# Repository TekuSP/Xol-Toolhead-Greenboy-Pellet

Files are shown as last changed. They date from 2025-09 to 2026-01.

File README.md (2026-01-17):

[][cc-by-nc-sa]

# Xol Toolhead
Xol Toolhead is the evolution of 'Mantis Xol 2' (<https://github.com/Armchair-Engineering/Mantis-Xol>).<br/>
Aimed at modularity and quality of life improvements for installation and serviceability.<br/>
We have left the mantis carriage behind, and thus are now just Xol sans Mantis. Don't worry, it's still a bit ugly. We wouldn't fix that..<br/>

This is fork for **Greenboy3D Pellet Extruder.** More about extruder here: https://greenboy3d.de <br/>

Project lead: ko-fi (https://ko-fi.com/O5O5OCC0K) [DW-Tas](https://github.com/DW-Tas)
Fork lead:  [TekuSP](https://github.com/TekuSP)

Join me on Discord (https://discord.gg/armchairengineeringsux)

Chat with me, fork owner on Discord: @TekuSP there



## Go to the /docs
All of the documentation has been moved to /docs to help keep the repo organised (crazy I know) and enable future things.
* [Full README](docs/README.md)
  * [Bill of Materials (BOM)](docs/BOM.md)
  * [Printing parts](docs/printing.md)
  * [Carriage assembly](docs/xol_carriage_assembly.md)
  * [Toolhead assembly](docs/toolhead_assembly.md)

<br/><br/>
You can help support the development of Armchair projects.<br/>
Donate at https://ko-fi.com/armchair<br/>
ko-fi (https://ko-fi.com/armchair)
<br/> <br/>

This work is licensed under a
[Creative Commons Attribution-NonCommercial-ShareAlike 4.0 International License][cc-by-nc-sa].

[][cc-by-nc-sa]

[cc-by-nc-sa]: http://creativecommons.org/licenses/by-nc-sa/4.0/
[cc-by-nc-sa-image]: https://licensebuttons.net/l/by-nc-sa/4.0/88x31.png
[cc-by-nc-sa-shield]: https://img.shields.io/badge/License-CC%20BY--NC--SA%204.0-lightgrey.svg

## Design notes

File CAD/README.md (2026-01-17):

The custom STLs that enable support for the Annex Double Folded Ascender are derived from an Annex Engineering design, they are bound by their license.
<br/><br/>
Additionally, the "assembly guide" CAD contains a mod of the Anex Sherpa-Mini which is also bound by their license.
<br/><br/>

Additionally, the "assembly guide" CAD contains a mod of the Greenboy3D pellet extruder model which is also bound by their license.
<br/><br/>The License Agreement for these "products" can be found here: https://github.com/Annex-Engineering/ANNEX-Engineering-License-Agreement
<br/><br/>
Product pages for these products can be found at:

* https://github.com/Annex-Engineering/Folded_Ascender-Extruder
* https://github.com/Annex-Engineering/Sherpa_Mini-Extruder
* https://wiki.greenboy3d.de/docs/Getting%20Started

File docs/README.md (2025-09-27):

[][cc-by-nc-sa]

# Xol Toolhead
Xol Toolhead is the evolution of 'Mantis Xol 2' (<https://github.com/Armchair-Engineering/Mantis-Xol>).<br/>
Aimed at modularity and quality of life improvements for installation and serviceability.<br/>
We have left the mantis carriage behind, and thus are now just Xol sans Mantis. Don't worry, it's still a bit ugly. We wouldn't fix that.

Project lead: ko-fi (https://ko-fi.com/O5O5OCC0K) [DW-Tas](https://github.com/DW-Tas)

Join me on Discord (https://discord.gg/armchairengineeringsux)



## What's new
`Xol-Toolhead Release [2024-06-19]`
### Major update
* Quality of life improvements
  * Toolhead
    * Combined multiple printed parts to simplify assembly
    * No more M2 or M2.5 heatset inserts
    * Part cooling fans slide into the top of the ducts are are secured with 2x M2.5x8 SHCS per fan
      * Hardware reduced from 8x M2 heatsets + 8 M2 screws to just 4 M2.5 screws
    * HE Fan now uses 4x M2.5x16 SHCS (previous M2.5x20 should still work)
    * All four hotend mounting screws can now be used with Rapido and Dragon UHF when using Sherpa-Mini Extruder
  * Carriage
    * Xol Carriage is now a single piece print
    * Belt clips are now the Archetype belt clip system
    * Internal path added for probe wires
* BOM changes
  * Toolhead
    * Removed:
      * M2 and M2.5 heatsets (except for X endstop)
      * M2 Screws (except for X endstop)
    * Extruder mount front 2 SHCS now 16mm (previously 20mm)
  * Carriage
    * All versions now attach to MGN rail with M3x8 SHCS (MGN12 previously required M3x6 BHCS)
    * Archetype belt clips require 4mm OD, 0.45mm wall width tube
      * 2x 22.5mm lengths
      * 'Has been tested with 4/3mm PTFE tube and seems OK but harder to install'
    * Belt pins are now all M3x30 for all carriage/belt combinations
      * Cut down screws now OK due to the metal tube protecting the belts
    * Added:
      * Large M3 washers and 2x M3x8 SHCS for MGN Carriage clamps (not optional, required for carriage strength)
* Tool Requirement
  * Tightening the M3 SHCS of the toolhead "feet" to the carriage requires a M2.5 ball head hex driver. `This is due to the requirement to tighten these screws from a slight angle.`
<details>
<summary><strong>Previous updates</strong> [click to expand]</summary>
<br/>

`Xol-Toolhead Release 2023-12-21`
[Historic Repo Link](https://github.com/Armchair-Heavy-Industries/Xol-Toolhead/tree/b5e52d79f11106338cad1ea619fc55be004061d5)
* Quality of life improvements
  * Cable routing holes are now on both sides of the toolhead
  * Cable routing holes can now fit MF3.0 commonly used on hotends
  * Awkward M3 Heatset insert replaced with easier to install M3 hex nut for front extruder mount connection
  * Rapido hotend mounting points rotated to improve wire routing
* Minimal BOM change
  * 1x M3 Hex Nut replaces 1x M3 Heatset Insert
  * 1x M3x6 BHCS replaces 1x M3x8 BHCS
* Reworked Extruder mount to Hotend mount interface
  * Old Hotend mounts will not work with new Extruder mounts and vice-versa

`Xol-Toolhead Release 2023-09-15`
[Historic Repo Link](https://github.com/Armchair-Heavy-Industries/Xol-Toolhead/tree/18acdc784e08c6703e5be316338cb8c8f26e0477)
* Modular approach to hotend mounts and extruders
  * Hotend mounts and extruder mounts are now separate parts
  * Extruder mounts incorporate the old Xol-Carriage or TAP adapter plates (same number of printed parts overall)
  * "Xol with bones" option: Add some screws for extra rigidity in the hotend mount
* Minimal BOM change
  * 1x M3x8 BHCS
  * 1x M3 Heatset
  * Optional "bones"
    * 2x M2x30 SHCS
    * 2x M2 Heatset
* Xol-Carriage update
  * Stronger belt clips
  * bigger probe cable channel with cable tie slot

`Xol-Toolhead Release 2023-07-14`
[Historic Repo Link](https://github.com/Armchair-Heavy-Industries/Xol-Toolhead/tree/bd63772155dfab692449fd498208c855561d44cf)
* Standardised hotend mounts around the Voron Design CW2/TAP carriage bolt hole pattern.
  * This approach reduces the number of hotend mounts and ducts by half - You don't have to search for TAP or non-TAP and we don't have to maintain twice as many parts
* Xol-Carriage
  * A new carriage built for Xol-Toolhead
  * Uses metal pins and a belt clip to secure the belts instead of having them squashed between mgn9/12 carriage and toolhead carriage
  * Improved serviceability - remove the toolhead from the carriage without disassembly in the printer. Unless you use Voron TAP or refuse to buy M2.5 hardware for Xol Carriage. Buy the m2.5 hardware, it's worth it trust us.
  * Modular probe mounting system - change probes without changing the whole carriage _`*Except for KlickyNG`_
* These carriage changes mean you can use any carriage that a Stealthburner bolts onto. (Our Xol-Carriage, or the stock voron carriage even.)
</details>

## Supported hardware
### Hotends
* Chube Compact
* Rapido HF
* Rapido UHF
* DropEffect XG
* DropEffect NeXtG
* Red Lizard K1-UHF
* Dragon UHF / UHF-Mini
* Dragon Standard / High Flow
* Dragon Ace
* Revo Voron
* NF-Crazy Volcano (or standard with v6 melt zone extender) `NF-Crazy with standard wide block no longer supported without extender`
* Others via User mods including [Bambulab](https://github.com/Armchair-Heavy-Industries/Armchair-Usermods/tree/main/files/Xol-Toolhead/BambuLab_Xol_HE_Mount)

### Extruders
* Sherpa-Mini
* Annex Double Folded Ascender
* Galileo G2SA *
* WristWatch G2 *
* WristWatch BMG
* Escapement (experimental)
* Vz-Hextrudort-Low
* LGX-Lite
* Orbiter v2.0

`⚠️ * G2SA and WWG2 not compatible with XolPAP `

### Probes
* PCB Klicky
* Klicky
* Beacon (Normal)
* Euclid
* Voron Design TAP `For RC8+ we suggest to use m3x50 BHCS instead of SHCS`<br/>
* BTT Eddy
* ⚠️ _KlickyNG support has been removed in this release_

### X-Rail/Belts
* MGN12H - 6mm Belts
* MGN12H - 9mm Belts
* MGN9H - 6mm Belts
* MGN9H - 9mm Belts

> [!WARNING]
> ## Front Idlers  
> Xol-Toolhead can collide with the stock voron front idlers for Trident and 2.4 when the toolhead is in the front corners of the build area. This can cause also issues with the homing sequence when homing X if the toolhead is at the front of the gantry on Y. <br/><br/>
> Fully compatible idlers:<br/>
> * clee's [BFI (Beefy Front Idlers)](https://github.com/clee/VoronBFI)  <br/>
> * Ramalama2's [Front Idlers](https://github.com/Ramalama2/Voron-2-Mods/tree/main/Front_Idlers)  

<br/>

> [!IMPORTANT]
> We've made some instructions for printing and assembly.  
> They took ages to make, please read them.  
> * [Bill of Materials (BOM)](BOM.md)  
> * [Printing parts](printing.md)  
> * [Carriage assembly](xol_carriage_assembly.md)  
> * [Toolhead assembly](toolhead_assembly.md)  
> * [LED Harness](led_harness.md)

## Acknowledgements
* [DW-Tas](https://github.com/DW-Tas) for giving Xol the giant refresh it needed.
* [CorvidBuilds](https://github.com/CorvidBuilds) for Xol1 and Xol2, the predecessors to this project.
* [Long/Mandryd](https://github.com/mandryd/VoronUsers/tree/master/printer_mods/Long/Mantis_Dual_5015) for the Mantis toolhead.
* [Derpimus](https://github.com/lraithel15133) for the exegesis, some CAD work, feedback, and just being a rad dude.
* [KayosMaker](https://github.com/KayosMaker) for the CAN board mounts and spacers.
* [JosAr](https://github.com/jlas1/Klicky-Probe) for Klicky.
* [WhoppingPochard](https://github.com/tanaes) and [VinnyCordeiro](https://github.com/VinnyCordeiro/) for PCB Klicky.
* [Nionio6915](https://github.com/nionio6915/Euclid_Probe) for Euclid.
* [VoronDesign](https://github.com/VoronDesign) for this particular CoreXY flavor.
* [AnnexEngineering](https://github.com/Annex-Engineering) for the Sherpa Mini and Double Folded Ascender extruders, and the K3 that influenced the air management of the ducts. And also for giving access to an early revision of the DFA so it could be adapted for this toolhead.
* [clee](https://github.com/clee), you know what you did.

<br/><br/>
You can help support the development of Armchair projects.<br/>
Donate at https://ko-fi.com/armchair<br/>
ko-fi (https://ko-fi.com/armchair)
<br/> <br/>

This work is licensed under a
[Creative Commons Attribution-NonCommercial-ShareAlike 4.0 International License][cc-by-nc-sa].

[][cc-by-nc-sa]

[cc-by-nc-sa]: http://creativecommons.org/licenses/by-nc-sa/4.0/
[cc-by-nc-sa-image]: https://licensebuttons.net/l/by-nc-sa/4.0/88x31.png
[cc-by-nc-sa-shield]: https://img.shields.io/badge/License-CC%20BY--NC--SA%204.0-lightgrey.svg

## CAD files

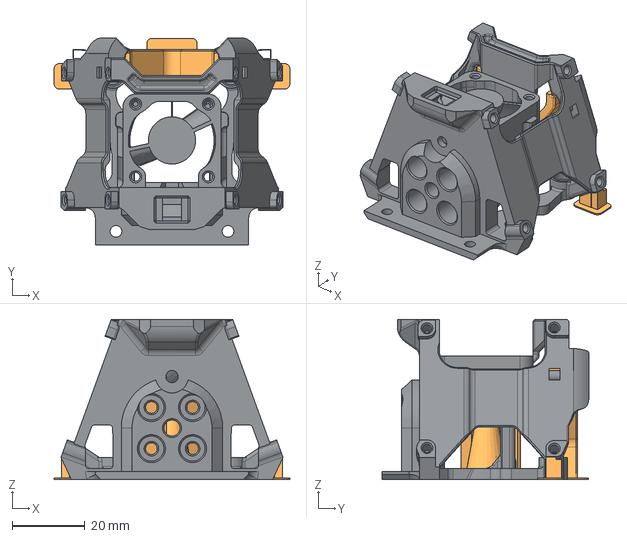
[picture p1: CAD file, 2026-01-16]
CAD/parts/Xol_HE_Chube-Compact_XolPAP.step
64.9 x 56.8 x 44.0 mm

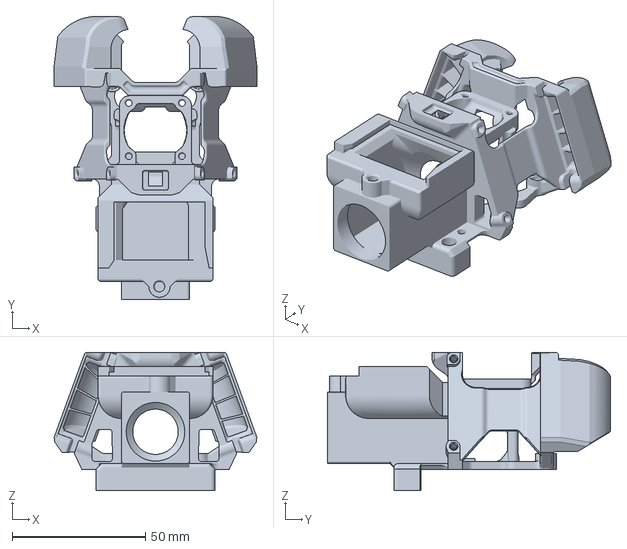
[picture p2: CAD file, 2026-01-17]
STL/Extruder Mounts/Xol Extruder Mount - Greenboy3D Pellet Extruder.3mf
76.2 x 106.3 x 52.0 mm

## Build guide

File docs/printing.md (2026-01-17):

# Printing Xol Parts

### Xol parts are not scaled to suit any particular filament. You will need to calibrate your printer/filament appropriately before printing Xol Parts

It is recommended to print a calibration part of a known size and adjust slicer shrinkage compensation.

### Printer tuning
Making Xol easier to assemble also meant making the main hotend mount part a more difficult print. You will need to have a reasonably well callibrated printer (although it was tested on a barely tuned Ender 3). <br/>
Some things in particular to note:
* Support removal `If you're printing too hot or with insufficient cooling the built in supports may be difficult to remove.`
* Overhangs `They're not too steep, but will be a problem if you're not printing your perimeters "inside to outside".`
* Wall widths `Some of the supports have a built in "interface" layers. Make sure your printer profile allows printing of walls down to at least 0.4mm. Check that you can see them in your slicer before you print them. DO NOT use walls wider than 0.55mm`

## What to print
There are many combinations of carriages/hotends/extruders that can be used with Xol. The tables below outline what you should print.

### Carriage
#### Xol Carriage
Pick the parts you need from the lists below and follow the instructions in [xol_carriage_assembly.md](xol_carriage_assembly.md) to build.

Carriage Size
* MGN12H: [Xol-Carriage_MGN12H.stl](../STL/Xol-Carriage/Xol-Carriage_MGN12H.stl)
* MGN9H: [Xol-Carriage_MGN9H.stl](../STL/Xol-Carriage/Xol-Carriage_MGN9H.stl)
* MGN9H (Front rail Printers for Ants [PFA]): [Xol-Carriage_MGN9H_PFA.stl](../STL/Xol-Carriage/Xol-Carriage_MGN9H_PFA.stl)

Belt Width
* 6MM: [[a]_belt_clamp_6mm_x2.stl](../STL/Xol-Carriage/[a]_belt_clamp_6mm_x2.stl)
* 9MM: [[a]_belt_clamp_9mm_x2.stl](../STL/Xol-Carriage/[a]_belt_clamp_9mm_x2.stl)
* 6MM (Front rail Printers for Ants [PFA]): [[a]_belt_clamp_6mm_PFA_x2.stl](../STL/Xol-Carriage/[a]_belt_clamp_6mm_PFA_x2.stl)

Probe Modules
* Pick the module to match your supported probe from the [Probe Modules](<../STL/Xol-Carriage/Probe Modules>) folder. <br/>
`Probe length should match the hotend length (standard or UHF)`

#### Voron Design TAP
Follow instructions from Voron Design <br /> _`For TAP RC8, replace the M3x50 SCHS with M3x50 BHCS to avoid bed clearance issues with regular length Xol Ducts`_

### Hotend and extruder hybrid Mount

| Hotend | 4010 Blower | XolPAP (Remote Cooling) | Duct Length (for probe module / XolPAP) |
| --- | --- | --- | --- |
| Greenboy3D Pellet Extruder | [Xol Extruder Mount - Greenboy3D Pellet Extruder.3mf](<../STL/Xol Extruder Mount - Greenboy3D Pellet Extruder.3mf>) | --- | UHF |

### Hotend Mount
Pick one option from the table below, depending of if you're using 4010 blower fans or remote cooling (XolPAP) for part cooling.

| Hotend | 4010 Blower | XolPAP (Remote Cooling) | Duct Length (for probe module / XolPAP) |
| --- | --- | --- | --- |
| Chube Compact | [Xol_HE_Mount-Chube-Compact_Fan.stl](<../STL/HE Mounts/Xol_HE_Mount-Chube-Compact_Fan.stl>) | [Xol_HE_Mount-Chube-Compact_XolPAP.stl](<../STL/HE Mounts/Xol_HE_Mount-Chube-Compact_XolPAP.stl>) | Standard |
| Rapido HF | [Xol_HE_Mount-Rapido_HF_Fan.stl](<../STL/HE Mounts/Xol_HE_Mount-Rapido_HF_Fan.stl>) <br/><br/> [Xol_HE_Mount-Rapido_v2_HF_Fan.stl](<../STL/HE Mounts/Xol_HE_Mount-Rapido_v2_HF_Fan.stl>) | [Xol_HE_Mount-Rapido_HF_XolPAP.stl](<../STL/HE Mounts/Xol_HE_Mount-Rapido_HF_XolPAP.stl>) <br/><br/> [Xol_HE_Mount-Rapido_v2_HF_XolPAP.stl](<../STL/HE Mounts/Xol_HE_Mount-Rapido_v2_HF_XolPAP.stl>) | Standard |
| Rapido UHF | [Xol_HE_Mount-Rapido_UHF_Fan.stl](<../STL/HE Mounts/Xol_HE_Mount-Rapido_UHF_Fan.stl>) <br/><br/> [Xol_HE_Mount-Rapido_v2_UHF_Fan.stl](<../STL/HE Mounts/Xol_HE_Mount-Rapido_v2_UHF_Fan.stl>) | [Xol_HE_Mount-Rapido_UHF_XolPAP.stl](<../STL/HE Mounts/Xol_HE_Mount-Rapido_UHF_XolPAP.stl>) <br/><br/> [Xol_HE_Mount-Rapido_v2_UHF_XolPAP.stl](<../STL/HE Mounts/Xol_HE_Mount-Rapido_v2_UHF_XolPAP.stl>) | UHF |
| DropEffect XG | [Xol_HE_Mount-XG_Fan.stl](<../STL/HE Mounts/Xol_HE_Mount-XG_Fan.stl>) | [Xol_HE_Mount-XG_XolPAP.stl](<../STL/HE Mounts/Xol_HE_Mount-XG_XolPAP.stl>) | Standard |
| DropEffect NeXtG (without extender) | [Xol_HE_Mount-DragonSF-HF_Fan.stl](<../STL/HE Mounts/Xol_HE_Mount-DragonSF-HF_Fan.stl>) | [Xol_HE_Mount-DragonSF-HF_XolPAP.stl](<../STL/HE Mounts/Xol_HE_Mount-DragonSF-HF_XolPAP.stl>) | Standard |
| DropEffect NeXtG (with extender) | [Xol_HE_Mount-DragonUHF_Mini_Fan.stl](<../STL/HE Mounts/Xol_HE_Mount-DragonUHF_Mini_Fan.stl>) | [Xol_HE_Mount-DragonUHF_Mini_XolPAP.stl](<../STL/HE Mounts/Xol_HE_Mount-DragonUHF_Mini_XolPAP.stl>) | Standard |
| Red Lizard K1-UHF | [Xol_HE_Mount-Rapido_UHF_Fan.stl](<../STL/HE Mounts/Xol_HE_Mount-Rapido_UHF_Fan.stl>) | [Xol_HE_Mount-Rapido_UHF_XolPAP.stl](<../STL/HE Mounts/Xol_HE_Mount-Rapido_UHF_XolPAP.stl>) | UHF |
| Dragon UHF | [Xol_HE_Mount-DragonUHF_Fan.stl](<../STL/HE Mounts/Xol_HE_Mount-DragonUHF_Fan.stl>) | [Xol_HE_Mount-DragonUHF_XolPAP.stl](<../STL/HE Mounts/Xol_HE_Mount-DragonUHF_XolPAP.stl>) | UHF |
| Dragon UHF-Mini (extender removed)  | [Xol_HE_Mount-DragonUHF_Mini_Fan.stl](<../STL/HE Mounts/Xol_HE_Mount-DragonUHF_Mini_Fan.stl>) | [Xol_HE_Mount-DragonUHF_Mini_XolPAP.stl](<../STL/HE Mounts/Xol_HE_Mount-DragonUHF_Mini_XolPAP.stl>) | Standard |
| Dragon Standard / High Flow | [Xol_HE_Mount-DragonSF-HF_Fan.stl](<../STL/HE Mounts/Xol_HE_Mount-DragonSF-HF_Fan.stl>) | [Xol_HE_Mount-DragonSF-HF_XolPAP.stl](<../STL/HE Mounts/Xol_HE_Mount-DragonSF-HF_XolPAP.stl>) | Standard |
| Dragon Ace (without extender) | [Xol_HE_Mount-Dragon-Ace_Fan.stl](<../STL/HE Mounts/Xol_HE_Mount-Dragon-Ace_Fan.stl>) | [Xol_HE_Mount-Dragon-Ace_XolPAP.stl](<../STL/HE Mounts/Xol_HE_Mount-Dragon-Ace_XolPAP.stl>) | Standard |
| Dragon Ace (with extender) | [Xol_HE_Mount-Dragon-Ace_Extender_Fan.stl](<../STL/HE Mounts/Xol_HE_Mount-Dragon-Ace_Extender_Fan.stl>) | [Xol_HE_Mount-Dragon-Ace_Extender_XolPAP.stl](<../STL/HE Mounts/Xol_HE_Mount-Dragon-Ace_Extender_XolPAP.stl>) | UHF |
| Dragon Ace Volcano (with extender)<br/>`Use included 3mm spacer` | [Xol_HE_Mount-DragonUHF_Fan.stl](<../STL/HE Mounts/Xol_HE_Mount-DragonUHF_Fan.stl>) | [Xol_HE_Mount-DragonUHF_XolPAP.stl](<../STL/HE Mounts/Xol_HE_Mount-DragonUHF_XolPAP.stl>) | UHF |
| Dragon Ace Volcano (No extender)<br/>`Use included 3mm spacer`  | [Xol_HE_Mount-DragonUHF_Mini_Fan.stl](<../STL/HE Mounts/Xol_HE_Mount-DragonUHF_Mini_Fan.stl>) | [Xol_HE_Mount-DragonUHF_Mini_XolPAP.stl](<../STL/HE Mounts/Xol_HE_Mount-DragonUHF_Mini_XolPAP.stl>) | Standard |
| Revo Voron | [Xol_HE_Mount-Revo-Voron_Fan.stl](<../STL/HE Mounts/Xol_HE_Mount-Revo-Voron_Fan.stl>) | [Xol_HE_Mount-Revo-Voron_XolPAP.stl](<../STL/HE Mounts/Xol_HE_Mount-Revo-Voron_XolPAP.stl>) | Standard |
| NF-Crazy Volcano | [Xol_HE_Mount-NF-Crazy_Volcano_Fan.stl](<../STL/HE Mounts/Xol_HE_Mount-NF-Crazy_Volcano_Fan.stl>) | [Xol_HE_Mount-NF-Crazy_Volcano_XolPAP.stl](<../STL/HE Mounts/Xol_HE_Mount-NF-Crazy_Volcano_XolPAP.stl>) | UHF |

#### XolPAP Ducts
If you're using XolPAP remote cooling, you will need either standard or UHF length ducts:
* Standard: [XolPAP Standard Length Duct.stl](<../STL/XolPAP ducts/XolPAP Standard Length Duct.stl>)
* UHF: [XolPAP UHF Length Duct.stl](<../STL/XolPAP ducts/XolPAP UHF Length Duct.stl>)

`⚠️ * G2SA and WWG2 extruders not compatible with XolPAP `

### Extruder Mount

Pick one extruder mount from the table below to match your extruder, and if it's going on Xol-Carriage or on TAP/Voron carriage.

| Extruder | Xol-Carriage | TAP / Voron Carriage |
| --- | --- | --- |
| Sherpa-Mini / <br/> Sharkfin  <br/>`K-face plate and optional` <br/> `short idler arm for Sherpa-Mini ` <br/> `from Annex Engineering`<br/> [Sherpa front k-face](<https://github.com/Annex-Engineering/Sherpa_Mini-Extruder/blob/master/STLs/optional_parts/%5Ba%5D_housing_front_k_x1_rev15.STL>) <br/> [Sherpa short idler arm](<https://github.com/Annex-Engineering/Sherpa_Mini-Extruder/blob/master/STLs/optional_parts/%5Ba%5D_idler_arm_short_x1_rev16a.STL>) | [Xol Extruder Mount - Sherpa-Mini.3mf](<../STL/Extruder Mounts/Xol Extruder Mount - Sherpa-Mini.3mf>) | [Xol Extruder Mount - Sherpa Mini - TAP.3mf](<../STL/Extruder Mounts/Xol Extruder Mount - Sherpa Mini - TAP.3mf>) |
| Annex Double Folded Ascender | [Xol Extruder Mount - DFA.stl](<../STL/Extruder Mounts/Xol Extruder Mount - DFA.stl>) <br/> *License [Note](<DFA_MOD_License.md>) | Not Supported |
| Vz-Hextrudort-Low / <br/> LGX-Lite | [Xol Extruder Mount - VZ-Hex+LGX-L.stl](<../STL/Extruder Mounts/Xol Extruder Mount - VZ-Hex+LGX-L.stl>) | [Xol Extruder Mount - VZ-Hex+LGX-L - TAP.stl](<../STL/Extruder Mounts/Xol Extruder Mount - VZ-Hex+LGX-L - TAP.stl>) |
| Galileo G2SA (Orbiter mount pattern) <br/> `NOT XolPAP Compatible` | [Xol Extruder Mount - G2SA.stl](<../STL/Extruder Mounts/Xol Extruder Mount - G2SA.stl>), AND <br/>  [G2SA front for Xol Extruder Mount.stl](<../STL/Extruder Mounts/G2SA front for Xol Extruder Mount.stl>) | [Xol Extruder Mount - G2SA - TAP.stl](<../STL/Extruder Mounts/Xol Extruder Mount - G2SA - TAP.stl>) , AND <br/>  [G2SA front for Xol Extruder Mount.stl](<../STL/Extruder Mounts/G2SA front for Xol Extruder Mount.stl>) |
| WristWatch G2 (Orbiter mount pattern)  <br/> `NOT XolPAP Compatible` | [Xol Extruder Mount - G2SA.stl](<../STL/Extruder Mounts/Xol Extruder Mount - G2SA.stl>), AND <br/>  [WWG2 front for Xol Extruder Mount.stl](<../STL/Extruder Mounts/WWG2 front for Xol Extruder Mount.stl>) | [Xol Extruder Mount - G2SA - TAP.stl](<../STL/Extruder Mounts/Xol Extruder Mount - G2SA - TAP.stl>) , AND <br/>  [WWG2 front for Xol Extruder Mount.stl](<../STL/Extruder Mounts/WWG2 front for Xol Extruder Mount.stl>) |
| WristWatch BMG | [Xol Extruder Mount - G2SA.stl](<../STL/Extruder Mounts/Xol Extruder Mount - G2SA.stl>), AND <br/>  [WWBMG front for Xol Extruder Mount.stl](<../STL/Extruder Mounts/WWBMG front for Xol Extruder Mount.stl>) | [Xol Extruder Mount - G2SA - TAP.stl](<../STL/Extruder Mounts/Xol Extruder Mount - G2SA - TAP.stl>) , AND <br/>  [WWBMG front for Xol Extruder Mount.stl](<../STL/Extruder Mounts/WWBMG front for Xol Extruder Mount.stl>) |
| Escapement | [Xol Extruder Mount - Escapement.stl](<../STL/Extruder Mounts/Xol Extruder Mount - Escapement.stl>) | [Xol Extruder Mount - Escapement - TAP.stl](<../STL/Extruder Mounts/Xol Extruder Mount - Escapement - TAP.stl>) |
| Orbiter v2.0 | [Xol Extruder Mount - Orbiter V2.stl](<../STL/Extruder Mounts/Xol Extruder Mount - Orbiter V2.stl>) | [Xol Extruder Mount - Orbiter V2 - TAP.stl](<../STL/Extruder Mounts/Xol Extruder Mount - Orbiter V2 - TAP.stl>) |

 ### Faceplate
There's only one option for the faceplate now. If you don't want an LED in the status light area, print the "diffuser" in a contrasting colour to the main faceplate part to show off the Xol logo.
* [Faceplate.stl](../STL/Faceplate/Faceplate.stl)
* [[t] Logo LED diffuser.stl](<../STL/Faceplate/[t] Logo LED diffuser.stl>) `Clear/translucent for diffuser, or contrasting colour for no LED`

 #### EBB 36 Mount
 Print the EBB 36 mount for Xol-Carriage to suit your CAN or break-out board / extruder combination.<br/>
 `If you aren't using Xol-Carriage (TAP users) there are numerous EBB mounts availble like these from KayosMaker:`[CANboard_Mounts](https://github.com/KayosMaker/CANboard_Mounts)
| Extruder | Without strain relief | With strain relief|
|-----|---|---|
|Sherpa-Mini |[EBB36 Mount - Sherpa-Mini.stl](<../STL/EBB Mounts/EBB36 Mount - Sherpa-Mini.stl>)|[EBB36 Mount - Sherpa-Mini [strain relief].stl](<../STL/EBB Mounts/EBB36 Mount - Sherpa-Mini [strain relief].stl>) |
|WW-BMG |[EBB36 Mount - WWBMG.stl](<../STL/EBB Mounts/EBB36 Mount - WWBMG.stl>)|[EBB36 Mount -WWBMG [strain relief].stl](<../STL/EBB Mounts/EBB36 Mount -WWBMG [strain relief].stl>)
|DFA | {todo} | {todo} |
| Galileo 2SA | {todo} | {todo} |
| Escapement | {todo} | {todo} |
|VZ-Hextrudort-Low | [EBB36 Mount - VZ-Hextrudort-Low.stl](<../STL/EBB Mounts/EBB36 Mount - VZ-Hextrudort-Low.stl>) | [EBB36 Mount - VZ-Hextrudort-Low [strain relief].stl](<../STL/EBB Mounts/EBB36 Mount - VZ-Hextrudort-Low [strain relief].stl>) |
| LGX-Lite | {todo} | {todo} |
|Orbiter v2.0 | [EBB36 Mount - Orbiter2.0.stl](<../STL/EBB Mounts/EBB36 Mount - Orbiter2.0.stl>) | [EBB36 Mount - Orbiter2.0 [strain relief].stl](<../STL/EBB Mounts/EBB36 Mount - Orbiter2.0 [strain relief].stl>) |

### M2.5 Savers
 Add a little colour, and protect your delicate 4010 blower fans <br/>
* [[a]_M2.5_saver_x4.stl](../STL/Faceplate/[a]_M2.5_saver_x4.stl) `These aren't optional extras, you need them to protect your fans. Also the screw holes are too shalow without them`

### Trident stepper spacer
On some Trident printers, the leadscrews are slightly too high and may collide with the Xol ducts when the toolhead is at the very front corners of the printer (usually only the right side when homing at Y,0). <br/>
To avoid this colision, there is a spacer available on printables that will lower the leadscrew stepper motors: [https://www.printables.com/model/486638-voron-trident-z-steppers-spacers](https://www.printables.com/model/486638-voron-trident-z-steppers-spacers)

<br/><br/><br/><br/>

⬅ [BOM](BOM.md) - [Carriage assembly](xol_carriage_assembly.md) ➡

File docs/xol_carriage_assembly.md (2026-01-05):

# Xol Carriage Assembly
Xol Carriage Image

| Notes | Image |
| --- | --- |
| Get the carriage ready by installing <br /> * 5x M3 heatsets<br />* 4x M3 hex nuts |  <br/>  <br/>  |
| Attach your probe module with 2x M3x6 BHCS |  |
| Run the probe wires up the channel before you install the carriage on the MGN rail. Don't forget to keep them secure using the cable tie slots. |  |
| `Option`<br/>_*If you haven't yet converted to sensorless homing, your X-endstop switch can be attached to the back of the carriage._<br/><br/> Install the switch with 2x M2x10 self tapping screws |  |
| Put the carriage on the MGN rail with <br />4 M3x8 SHCS<br/> `M3x6 for CNC Xol-Carraige` |  |
| Use 2x M3x8 SHCS and 2x large M3 washers to 'clamp' the carriage to the MGN rail. `M3 + M5 washers can be stacked if you don't have the large M3 washers` |  <br/>  |
| Install the belts and tubes into the belt clips. It should look like the picture when installed correctly.<br/> `Left clip hidden to show the belt path inside the clip` <br/> <br/>  * Pull your belt through the belt clips.<br/>  * Make a loop and pinch together so that the teeth are locking together.<br/>  * Pull the belt back through the same hole in the clip.<br/>  * Repeat for the 2nd belt, leaving enough slack so you can slide the 4mm OD tube through the opening of the loops. <br/> * Pull the belts tight around the tube.<br/> * Use a small cable tie, or wire tie to pull the tube into the recess in the clip and hold it tight in position.<br/> * Tuck the excess belt back into the clip. |  |
| Push the belt/clip/tube assembly into the side of the carriage so that it lines up and you can push the M3x30 pin down from the top and through the tube. Repeat for the other side. |  |
| Tada!!! You have a completed Xol Carriage ready to attach the toolhead |  |

<br/><br/><br/><br/>
⬅  [Printed parts](printing.md) - [Toolhead assembly](toolhead_assembly.md) ➡

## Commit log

2025-09-27 fix printint.md chube compact links
2026-01-05 Update MGN rail installation instructions
    Clarified the screw specifications for the MGN rail installation.
2026-01-16 upload chube-compact HE mount STEP files
    [Xol_HE_Chube-Compact_XolPAP.step]
2026-01-17 Add Pellet Toolhead from Greenboy3D
    [Xol Extruder Mount - Greenboy3D Pellet Extruder.3mf]

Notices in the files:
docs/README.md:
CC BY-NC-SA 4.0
